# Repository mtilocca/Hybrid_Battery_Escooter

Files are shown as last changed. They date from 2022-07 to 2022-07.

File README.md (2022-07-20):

# Hybrid_Battery_Escooter
In this repository it is presented the work related to the B.sc. thesis, where an High Performance Hybrid Battery circuit was developed for an E-scooter.

In this project is presented a strategy aimed at the development of a DC-DC converter best suited to operate in an HESS configuration using HP and HE battery types in a Dual- cell architecture for E-scooter application.
The core feature of the active parallel HESS configuration proposed was represented by the development and testing of a bidirectional DC-DC converter. Which needs to operate either as a boost and either as a buck converter. Through that a 3- phase BLDC was supplied with the energy stored in the UC bank during accelerations of the ES, while it recharged the UC bank during regenerative braking.
It was first simulated the acceleration behavior of an ES. The parameters obtained from that were used for designing the DC- DC converter. According to its requirements a control algorithm was developed in Arduino. Consequently empirical tests were performed to validate the converter and the developed control algorithm.

## System Architecture 
HESS

HESSs

## PCB Schematics 
SCHEM

pcb

## Experimental Results 


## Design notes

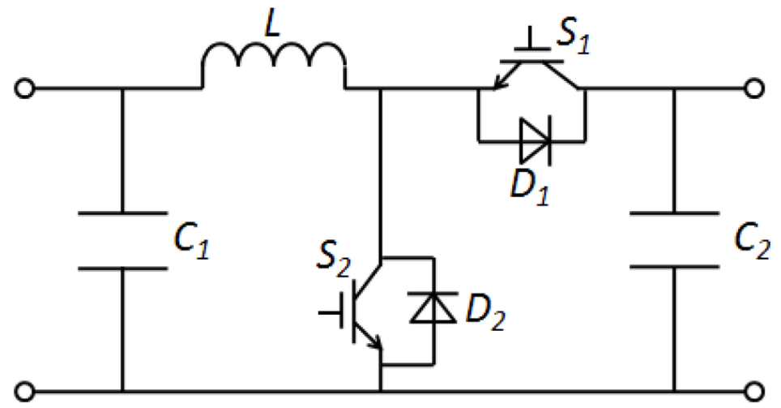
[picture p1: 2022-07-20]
Modeling/Buck Boost.PNG

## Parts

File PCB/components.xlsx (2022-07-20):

Type | PCB name | Value | Farnell code | quantity
connector |  |  | 3704683 (https://uk.farnell.com/phoenix-contact/1714955/terminal-block-wire-to-brd-2pos/dp/3704683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) | 6
connector |  |  | 3041165 (https://uk.farnell.com/phoenix-contact/1711725/terminal-block-wire-to-brd-2pos/dp/3041165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) | 9
capacitor | C4&C5&C6 | 2200u | ECA1JHG222 | 12
Mosfet |  |  | FQP85N06 (https://uk.farnell.com/infineon/irf640npbf/mosfet-n-200v-18a-to-220/dp/8648379?st=irf640) | 10
Mosfet driver | IR2110PBF |  | IR2110PBF (https://uk.farnell.com/intersil/el7104csz/driver-mosfet-single-high-speed/dp/1561928?st=el7104) | 8
connector |  |  | 31072102 | 6
capacitor | C1 & C2 | 470u | MCKSK100M471J32S (https://uk.farnell.com/united-chemi-con/ekyb800ell271mj30s/cap-270-f-80v-20/dp/2842025) | 10
Heatsink |  |  | 504222B00000G | 1
IC socket |  |  | 4814-3000-CP | 3
diode |  |  | 1N485B. | 5

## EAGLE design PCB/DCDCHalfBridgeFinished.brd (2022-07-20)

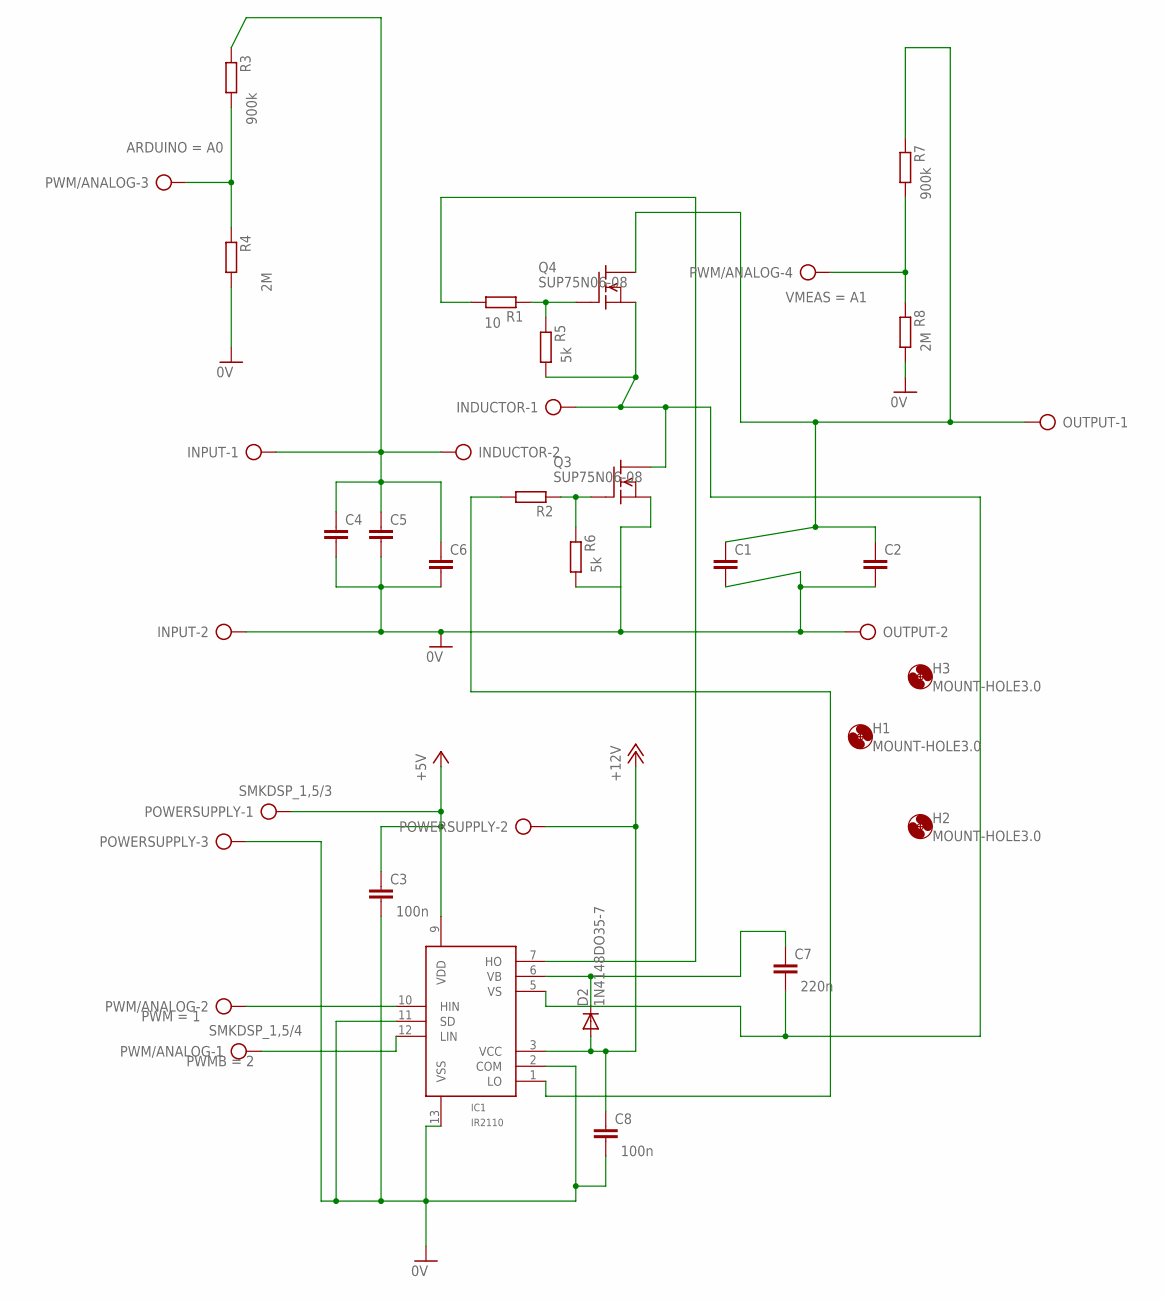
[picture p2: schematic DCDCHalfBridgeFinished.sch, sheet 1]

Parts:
C1, C2, C4, C5, C6: C-EU050-025X075; C050-025X075
C3, C7, C8: C-EU025-025X050; C025-025X050
D2: 1N4148DO35-7; DO35-7
H1, H2, H3: MOUNT-HOLE3.0; 3,0
IC1: IR2110; DIL14
INDUCTOR: AK300/2
INPUT: AK300/2
OUTPUT: AK300/2
POWERSUPPLY: SMKDSP_1,5/3
PWM/ANALOG: SMKDSP_1,5/4
Q3, Q4: SUP75N06-08; TO220
R1, R2, R3, R4, R5, R6, R7, R8: R-EU_0204/7; 0204/7

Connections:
+5V: C3.1, IC1.9 (VDD), POWERSUPPLY.1
+12V: C8.1, D2.A, IC1.3 (VCC), POWERSUPPLY.2
GND: C1.2, C2.2, C3.2, C4.2, C5.2, C6.2, C8.2, IC1.2 (COM), IC1.11 (SD), IC1.13 (VSS), INPUT.2, OUTPUT.2, POWERSUPPLY.3, Q3.3 (S), R4.2, R6.2, R8.2
unnamed: PWM/ANALOG.3, R3.2, R4.1
unnamed: IC1.12 (LIN), PWM/ANALOG.1
unnamed: IC1.10 (HIN), PWM/ANALOG.2
unnamed: C7.2, IC1.5 (VS), INDUCTOR.1, Q3.2 (D), Q4.3 (S), R5.2
unnamed: IC1.1 (LO), R2.2
unnamed: Q4.1 (G), R1.1, R5.1
unnamed: Q3.1 (G), R2.1, R6.1
unnamed: PWM/ANALOG.4, R7.2, R8.1
unnamed: C7.1, D2.C, IC1.6 (VB)
unnamed: C1.1, C2.1, OUTPUT.1, Q4.2 (D), R7.1
unnamed: IC1.7 (HO), R1.2
unnamed: C4.1, C5.1, C6.1, INDUCTOR.2, INPUT.1, R3.1

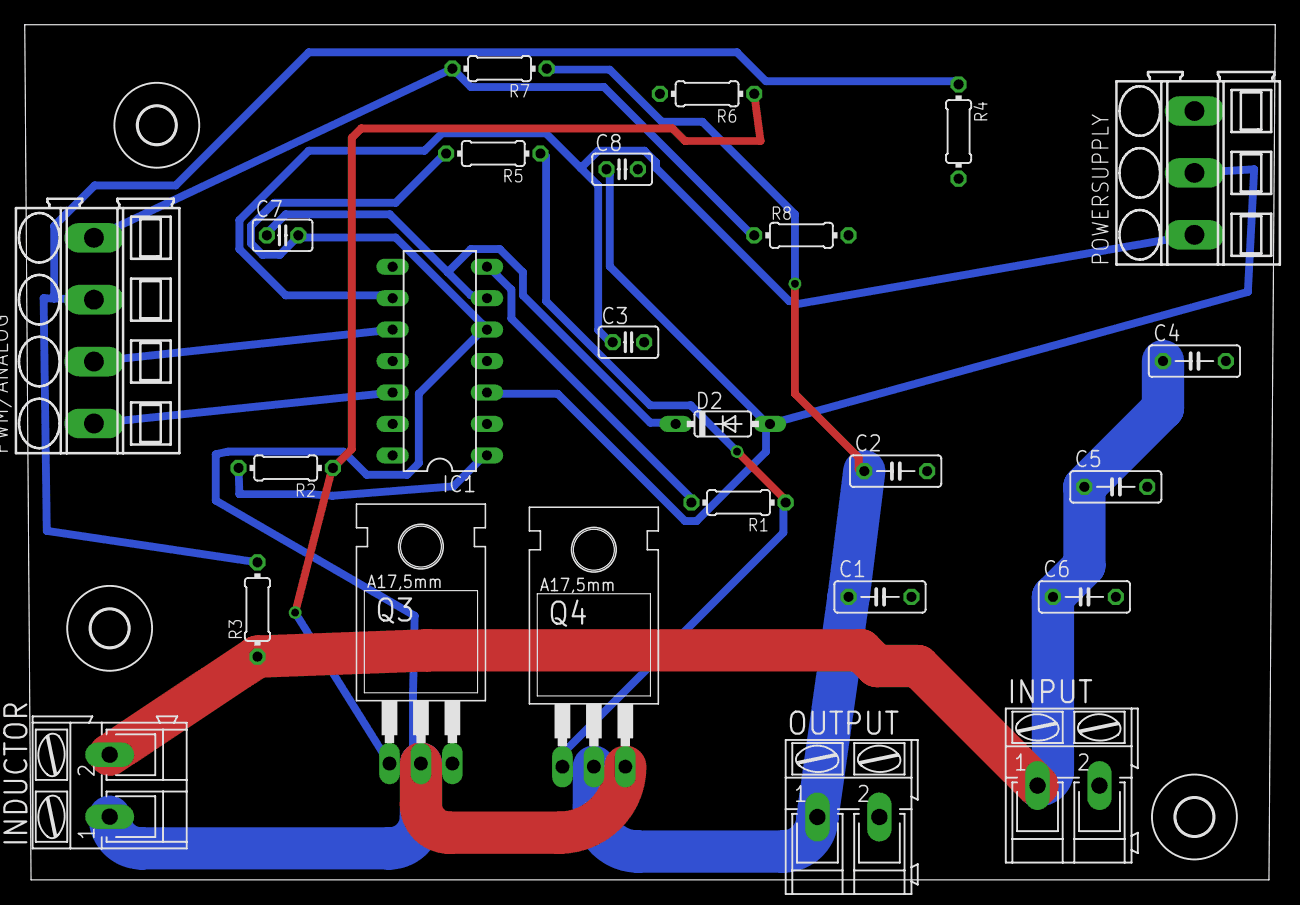
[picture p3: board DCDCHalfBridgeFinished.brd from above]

Board: 2 copper layers, 101.0 x 69.1 mm, 28 parts (0 on the bottom side), 15 nets.

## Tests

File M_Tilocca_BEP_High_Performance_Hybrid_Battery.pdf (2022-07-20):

# DC-DC converter for high performance hybrid battery applications

Mario Tilocca, Eindhoven University of Technology, Department of Electrical Engineering, ID 1034263, m.tilocca@student.tue.nl

Abstract—In this paper is presented a strategy aimed at the development of a DC-DC converter best suited to operate in an HESS configuration using HP and HE battery types in a Dual-cell architecture for E-scooter application.
The core feature of the active parallel HESS configuration proposed was represented by the development and testing of a bidirectional DC-DC converter. Which needs to operate either as a boost and either as a buck converter. Through that a 3-phase BLDC was supplied with the energy stored in the UC bank during accelerations of the ES, while it recharged the UC bank during regenerative braking.
It was first simulated the acceleration behavior of an ES. The parameters obtained from that were used for designing the DC-DC converter. According to its requirements a control algorithm was developed in Arduino. Consequently empirical tests were performed to validate the converter and the developed control algorithm.

Index Terms—E-Scooter, Hybrid Battery, HESS, Voltage Sensor, Lithium-ion Ultracapacitors, LiFePo4 battery, DC-DC converter, Half Bridge, Buck-Boost, PWM, Control Algorithm.

I. INTRODUCTION
I
N this paper is discussed about the development of a DC-DC converter which allows to integrate a dual battery architecture in E-scooters (ES) applications. The main contribution is to show an efficient energy management strategy aimed at developing and controlling a DC-DC bidirectional converter. The scope of the converter is to regulate the input and output voltage dynamically. Thus it is possible to ensure a constant output voltage, namely the nominal operating voltage of the BLDC motor used in ES, regardless of the value of the input voltage during ES accelerations. Conversely during regenerative braking the proposed control strategy enables the output voltage to vary according to the state of charge (SoC) of the high power (HP) battery topology. During this process the input voltage supplied is maintained constant throughout the duration in which the employed BLDC motor is operated as a generator. Therefore a research question arises:

What approach should be adopted when developing bidirectional DC-DC allowing to combine a dual battery architecture while ensuring to maintain high performances in ES applications ?

In the following sections of the paper it is discussed about related researches which focused on ES and battery topologies used in light electric vehicles applications. Consequently the methodologies employed and the results obtained during the development and testing of the DC-DC bidirectional converter are examined.

II. LITERATURE RESEARCH & BACKGROUND

ES are designed to be a quiet and low vibration vehicle that find their main employment in residential urban areas drastically reducing CO2 emissions and improving air quality
[1] .In recent years with the improvements in the field of a rechargeable batteries it has been possible to sensibly increase the operational range of light E-vehicles where volume constraints play a key role in the design of the E-bikes and ES particularly [2].
Therefore, one of the main challenges is developing a balanced system of different fuel-cell topologies which allows the vehicle to achieve performances and have an autonomy range comparable to scooter mounting an internal combustion engine keeping the total mass of the vehicle approximately the same.
In order to tackle this challenge a possible solution is the development of hybrid energy storage systems (HESSs) [3]. A typical HESS configuration is built using two different topologies of fuel-cells, being able to efficiently combine both High Energy (HE) and High Power (HP) characteristics [4]. In this research paper the goal is being able to develop DC-DC converter suited to operate in a Dual-Cell system which employs Lithium-Ion ultra-capacitors in particular for their HP properties together with Lithium Iron Phosphate (LiFePo4) for the HE part.
One of the main focuses is towards the charge/discharge energy efficiency which is one of the main indicators regarding the battery life cycle performance [4]. In order to achieve an higher overall efficiency of the system an important role is played by the handling of the energy during regenerative braking and standstill accelerations where the energy demand is higher compared to cruise speed.
During standstill accelerations the primary source of the energy drawn by the Brush-less DC motor of the vehicle are the lithium-ion ultracapacitors as the overall power demand in order to reach the cruise speed is high. Conversely during the part of the trip at constant speed the LiFePo4 batteries should be the main source of the energy drawn by the BLDC motor as the power demand is low but constant.
During regenerative braking the power flow is reversed, going from the BLDC motor to the fuel-cells. In this scenario the energy should be first directed to the ultracapacitors in order to recharge them [5]. Solely after the ultracapacitors are fully charged the power should be drawn by the LiFePo4 cathode battery pack as the latter has an higher internal resistance compared to the Lithium-Ion ultracapacitors. Therefore leading to higher losses which can overheat the battery damaging it. Hence in order to minimize the losses a DC-DC converter is placed between the ultracapacitors and the battery pack to allow a bidirectional power flow [6].

III. METHODS
A. Acceleration of an E-Scooter
The technology employed in the development of electric scooters have been steadily improving in recent years reaching performances analogous with the ones of internal combustion engine (ICE) scooters.
An important parameter of comparison between the ES and the ICE scooter is represented by the wide open throttle (WOT) behavior of the ES in a standstill acceleration. In order to comprehend this particular behavior a simulation of 500 data points was performed in Matlab. The constant parameters of the ES analyzed are depicted in Table I. Two separate equations were used in order to precisely simulate the behavior of the increase of velocity vn+1 of the ES according to: [2]

vn+1 = vn +δt ·(157−0.00145 · v

2
n
) | (1)

where vn is the current velocity, the aforementioned equation can be used to describe the behavior of the ES until it reaches a velocity of 10.8 m/s; afterwards Eq. 2 is used to calculate the next value of the velocity in the simulation [2].

vn+1 = vn +δt ·(7.30−0.53 · vn −0.00145 · v

2
n

) (2)

Consequently it is possible to progressively calculate the travelled distance dn+1 according to: [2]

dn+1 = dn +0.1 · vn | (3)

where, dn represents the current traveled distance. Since the ES simulation is at WOT it is assumed the acceleration a to be constant as it is depicted in the following equation:

a =

2 · dtot t
2 | (4)

where, dtot represents the total distance traveled by the scooter to reach its maximum velocity. Hence, it is possible to determine the behavior of the current drawn from the batteries by the 3-phase BLDC motor, Imotor according to Eq. 5. Thus, it is consequently possible to determine the development of traction force of the ES according to Eq. 6 [7].

Imotor =

avnm Vmotor | (5)

Ftr =

VmotorImotor

vn+1

(6)

B. Battery Topologies
In the system analyzed HP and HE battery topologies are combined together in an active parallel HESS configuration as it is shown in Fig. 1.

TABLE I
SCOOTER SIMULATION CONSTANTS
Symbol | Variable | Value | Unit
Vm | BLDC motor nominal voltage | 48 | V
m | total mass of the scooter | 180 | kg
t | total simulation time | 50 | s
δt | time sample | 0.1 | s

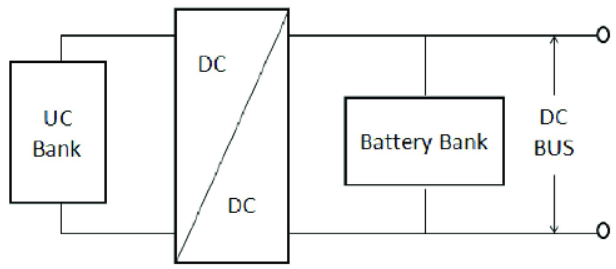
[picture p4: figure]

Fig. 1. Active parallel HESS configuration [3]

LiFePo4 cathode battery: Due to its low cost, long durability and more environmental friendly impact compared to cobalt based cathode batteries LiFePo4 have been chosen to be the HE components in the HESS configuration [8]. The specifications of a LiFePo4 fuel-cell are depicted in Table II. In order to meet the DC bus voltage requirements 16 fuel-cells are connected in series thus satisfying the nominal voltage requirement of the BLDC motor of the ES.
Thus the battery bank has a voltage ranging between 58.4 V and 40 V depending on the state of charge SoC of the battery bank.
Lithium-Ion Ultracapacitors: One of the main characteristics of the chosen ultracapacitors is their property to fully discharge in few seconds which makes them best suited to be used as source of power during accelerations of the ES [9]. Their HP characteristics are shown together with the main properties in Table III.
By contrast it is worth to note that the lithium-ion ultracapacitors have a lower energy density compared to the the LiFePo4. In the HESS configuration analyzed 10 Lithium-Ion ultracapacitors fuel-cells were connected in series, with a voltage ranging between 22 V and 38 V depending on the SoC. Which was constantly monitored via a voltage divider connected to the microcontroller.
C. DC-DC Converter
1) Converter Topologies: The main challenge in the development of an HESS configuration is the realization of a bidirectional DC-DC convert. Which allows the power to flow

TABLE II
LIFEPO4 CHARACTERISTICS [8]
Name | Value | Unit
Nominal cell voltage | 3.2 | V
Max charge voltage | 3.65 | V
Min discharge voltage | 2.5 | V
Specific Energy | 90110 | Wh/kg
Energy density | 220 | Wh/L
Specific Power | 200 | W/kg
Internal resistance | 0.1 | Ω

TABLE III
LITHIUM-ION ULTRACAPACITOR SPECIFICATIONS [9]
Name | Value | Unit
Nominal cell voltage | 2.2 -3.8 | V
Specific Energy | 11 | Wh/kg
Energy density | 19-25 | Wh/L
Specific Power | 9300 | W/kg
Internal resistance | 0.13 | Ω

TABLE IV
DC-DC CONVERTER CONSTANTS
Symbol | Variable | Value | Unit
VDC | DC bus nominal voltage | 48 | V
Vc | Ultracapacitors voltage range | 22-38 | V
fs | Switching frequency | 32000 | Hz
IDC | DC bus max current | 22.64 | A

either from the UC and battery banks to the BLDC motor and either during regenerative braking from the motor to the fuel-cells [10]. Thus creating a power buffer extends the life cycle of either the HP and HE components whilst shrinking the thermal losses.
In this particular case the DC-DC converter must work as a boost converter. Thus regulating the current UC bank voltage to the nominal DC bus voltage, during ES accelerations where the main energy source is provided by the UC bank. Conversely during braking the power recovered should be firstly directed to the UC bank until it is fully charged. Hence during this phase the DC-DC converter has to operate as a buck converter as the DC bus nominal voltage is higher than the maximum UC bank voltage, as it is shown in Table IV. For the aforementioned reasons the most suitable DC-DC converter for this application is a bidirectional buck-boost half bridge, as shown in Fig. 2.

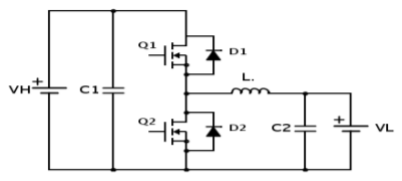
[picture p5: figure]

Fig. 2. Bidirectional Buck-Boost Half Bridge [10]

Boost Mode: When working as a boost converter, the power Mosfet Q1 shown in Fig. 2 is switched off for the whole duration of the process, while the power Mosfet Q2 is regulated according to the duty cycle Dboostobtained with the following equation:

Dboost = 1−

Vc

VDC

(7)

where Vc represents the input voltage, represented by the UC bank voltage and VDC the output voltage represented by the DC bus nominal voltage as it is shown together with the other converter constants in Table IV.

By knowing the duty cycle it is possible to design to determine the required inductance L1 using the following equation:

L1 =

VcDboost
fs∆IL

(8)

where fs represents the switching frequency and ∆IL the ripple current which can be obtained according to Eq. 9:

∆IL =

0.35 ·VDC ·IDC
Vc

(9)

where it is assumed that the ripple current is equal to 35% of the maximum output current IDC drawn by the BLDC motor. Moreover it is possible to calculate the required output capacitance C1 as shown in Eq. 10 where ∆Vrip represents the voltage ripple which is assumed to be maximum 1% of the total output voltage and it is calculated according to Eq. 11.

C1 =

IDCDboost

fs∆VripB

(10)

∆VripB = 0.01 ·VDC | (11)

Buck Mode: During regenerative braking it is assumed that the UC bank is empty as the energy in it should have been used previously during the acceleration phase.
Therefore the DC-DC converter works in buck mode in order to recharge the UC bank. Assuming a 100% efficiency it can be assumed that the power in input Pin is equal to the power in output Pout as shown in the following equations:
Pin = VDCIDC | (12)
Pin = Pout | (13)

by knowing the power in output it is possible to calculate the current which is drawn by the UC bank Ic during regenerative braking as shown in the following equation:

Ic =

Pout
Vc

(14)

During this phase the power Mosfet Q2 is switched off, while by knowing the duty cycle Dbuck as it is shown in Eq.15 of the power Mosfet Q1 showed in Fig. 2, it is possible to calculate the required inductance L2 through Eq. 16.

Dbuck =

Vc

VDC

(15)

L2 =

Vc ·(1−Dbuck)
2 · fsIc

(16)

Moreover the required output capacitance C2 can be calculated according to the following equation:

C2 =

DbuckIc

fs∆Vripb

(17)

where ∆Vripb
represents the voltage ripple which is estimated to account for 1% of the UC bank voltage as shown in the equation below.
∆Vripb = 0.01 ·Vc | (18)

D. Microcontroller Implementation & PWM Algorithm
In order to monitor the SoC of the UC bank and the voltage being supplied to or drawn by the DC bus two voltage sensors were be used. Hence two voltage dividers were directly implemented on the PCB which was connected with the employed Arduino Mega 2560. The chosen microcontroller can sense a maximum voltage of 5 V, any value above might cause irreparable damage. Therefore the resistors employed had a value of 1 kΩ and 12 kΩ respectively. Thus the microcontroller could safely sense voltages up to 65 V while maintaining an optimal current of 3.8 mA. By constantly being updated regarding the voltage of the UC bank and DC bus it was possible to estimate the SoC. Based on current SoC of the UC and DC bus the duty cycle Dboost of the power Mosfet Q2 was constantly adapted by sending a new pulse width modulation (PWM). As more power during accelerations is being drawn by the BLDC motor the voltage Vc of the UC bank is reduced and therefore the duty cycle Dboost increased.
Conversely during regenerative braking the duty cyle Dbuck was updated according to voltage of the UC bank Vc representing its SoC. Which gradually increased as the supercapacitors were being recharged.

IV. RESULTS & DISCUSSION

A. Acceleration of an E-scooter
By applying Eq.1 and Eq.2 into the Matlab tool the behavior of the velocity of the ES at WOT can be obtained as it is shown in Fig.3. In this figure it is shown how the maximum velocity obtained is around 48 km/h, which accurately represents the empirical behavior of scooters. Consequently, by applying Eq.3 and Eq.4 it was found that the acceleration a of the ES at WOT is equal to 0.483 m/s

2
. In Fig.4 it is shown the

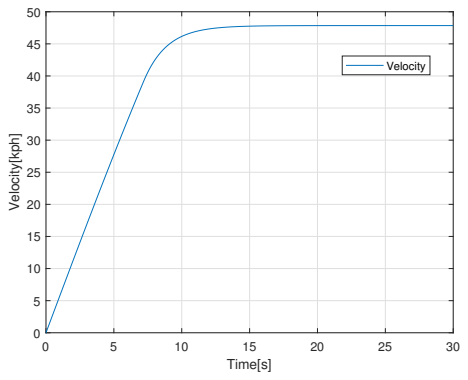
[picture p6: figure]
Time[s]; Velocity[kph]; Velocity

Fig. 3. Full power acceleration of ES

behavior of the current drawn by the BLDC motor of the ES which was obtained by applying Eq.5. It is worth mentioning that the behavior of velocity, shown in Fig.3, and the behavior of the motor current, shown in Fig. 4, are similar as they are both influenced by the acceleration a.
By comparing the velocity of the scooter and the current

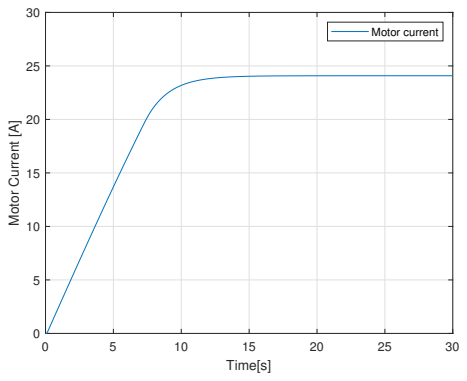
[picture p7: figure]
Time[s]; Motor Current [A]; Motor current

Fig. 4. Current drawn by the scooter motor during acceleration time

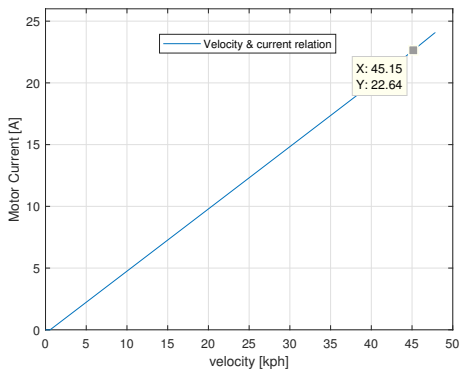
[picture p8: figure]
velocity [kph]; Motor Current [A]; Velocity & current relation

Fig. 5. Current drawn by the scooter motor with respect to velocity

drawn by its motor as it is shown in Fig.5 it is worth noting that they have a linear relation; furthermore from the aforementioned graph it was possible to determine the current drawn by the motor at 45 km/h which is the speed limit at which the scooters are allowed to drive in most EU countries. The value obtained from this graph was used as maximum motor current IDC in the DC-DC converter parameters calculations. Moreover by applying Eq.6 it was possible to simulate the

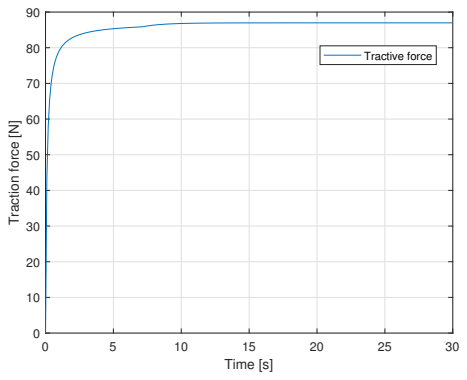
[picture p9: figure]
Time [s]; Traction force [N]; Tractive force

Fig. 6. Traction force behavior of ES at full power acceleration

TABLE V
DC-DC CONVERTER PARAMETERS
Symbol | Variable | Value | Unit
C1 | Boost output capacitance | 798 | µF
C2 | Buck output capacitance | 5600 | µF
L1 | Inductance boost | 21.5400 | µH
L2 | Inductance buck | 1.4498 | µH

behavior of the traction force Ftr of the ES as shown in Fig.6, it is worth noting that the force reaches in 10 seconds its peak value which is 87 N and it behaves steadily afterwards. The rapid growth above 80 N in less than 2 seconds has to be addressed to the constant acceleration at which the scooter is traveling. Consequently as the velocity of the scooter is higher than 10.8 m/s it slows its growth until it steadily increase to reach 87 N. Furthermore it is important to mention that the values of the traction force obtained in the simulation are similar with discrepancy of 0.34% to the gathered empirical data of a similar ES which reaches a speed of 35 km/h with a traction force of 86.7 N [7].

B. DC-DC Converter
In order to realize the DC-DC converter PCB using the software Eagle it was first needed to calculate the boost capacitance C1 and the buck capacitance C2 following Eq.10 and Eq.17 respectively as it is shown in TableV. Furthermore the respective inductors L1 for the boost mode and L2 for the buck mode were calculated according to Eq.8 and Eq.16. However since it is possible to mount only one inductor in the chosen design it was decided to build the inductor designed for the boost mode as it is larger than the minimal one needed for the buck mode as it is shown in Table V. In Fig.7 it is shown the circuitry schematics developed through the software Eagle, it was decided to use to satisfy the buck capacitance C2, 3 parallel connected ECA1JHG222 electrolytic capacitors with 2200 µF capacitance each. Whilst 2 parallel connected MCKSK100M471J32S electrolytic capacitors with 270 µF capacitance each for the boost capacitance C1.
The power Mosfet employed was the FQP85N06due to its high switching properties and its reliability at high voltages and currents. Moreover the FQP85N06 power Mosfets will receive the boosted PWM signal from the IR2110 gate driver which was connected directly to the Arduino Mega 2560. The final layout of the 2 layer PCB board designed is presented in Fig.8. The board high power traces were designed to be 0.018 mm thick and 7.62 mm wide in order to resist to a current up to 18 A. Whilst the traces concerning the gate driver and voltage dividers were designed to be 0.635 mm wide being resistant to a current up to 2.7 A. Furthermore two ground planes were designed having an minimal isolation of 1.27 mm from each trace.
V. TESTING
The proposed DC-DC converter design and control algorithm were empirically tested. In the experimental setup in addition to the Arduino Mega 2560 and the assembled PCB a 94 Ω resistor was employed as load to dissipate the

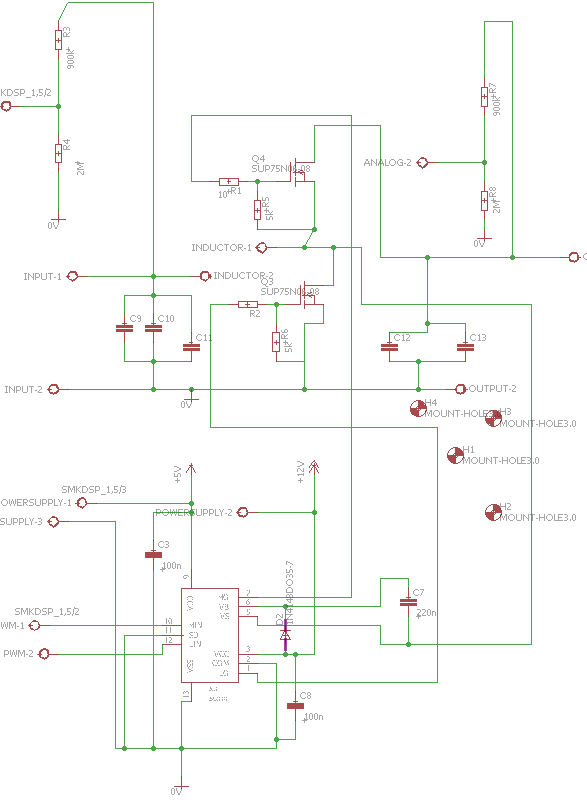
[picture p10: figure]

Fig. 7. Bidirectional buck-boost half bridge Eagle schematic

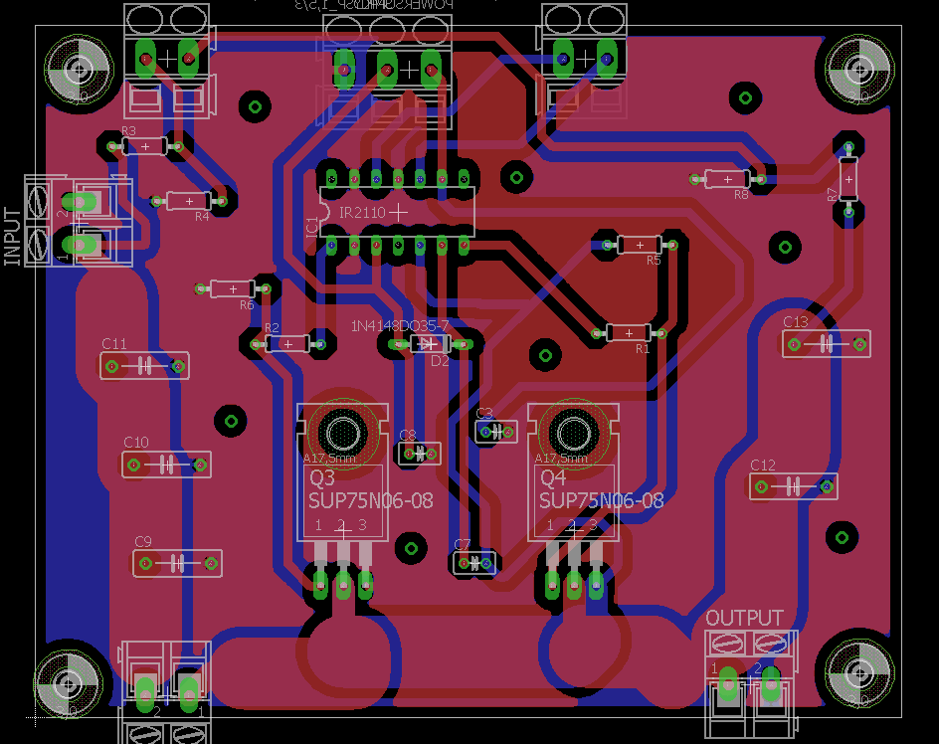
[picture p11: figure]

Fig. 8. Bidirectional buck-boost half bridge Eagle designed PCB

power while a DC voltage source was used to supply power to the circuit. Two external auxiliary DC voltage sources were employed in order to power the IR2110 gate driver. Furthermore the switching frequency was increased from 32 kHz to 62.5 kHz in order to enable higher reliability and lower losses.
Before tests involving the lithium-ion ultracapacitors could be conducted it was first tested that the converter worked in boost and buck mode with fixed duty cycles Dboost and Dbuck. In order to achieve the correct values the function which calculated the duty cycle in Arduino had to be adjusted and tuned. As these experiments were successful the control algorithm aimed at dynamically update the duty cycle could be tested. During Boost operation the DC-DC converter input voltage was gradually manually decreased ranging from 38 V to 22 V as it is shown in Fig.9.

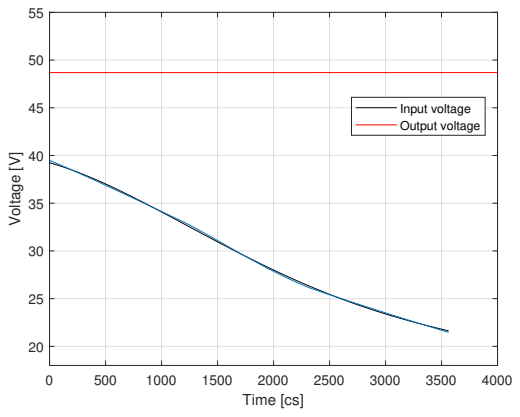
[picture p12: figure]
Time [cs]; Voltage [V]; Input voltage; Output voltage

Fig. 9. DC-DC converter input and output voltage fitted curves behavior during Boost operation

This was aimed at simulate the behavior of the ultracapacitors bank whose voltage is dropped as its SoC shrinks.
The output voltage behavior remained steady throughout the entire experiment as it is shown in Fig.9.
In this figure the behavior of the data recorded through the microcontroller has been processed in Matlab to obtain the fitted curves of the behavior of the input and output voltage. Conversely during buck operation as the power flow is reversed the input voltage is maintained steady at 48 V while the supercapacitors were being recharged. An offset 12.727% higher with respect to the initial voltage during buck operation (22 V) in the Arduino resolution was recorded as it is presented in Fig.10.
Thus during buck operation the UC bank was overcharged despite an input current of 0.82 A. Consequently this led to damaging the UC bank. However the behavior of the output voltage during buck operation shown in Fig. 10 followed the theoretical expectations as it gradually increased as the SoC of the UC bank incremented.
Hence, despite the boost operation of the converter could not be tested with the UC bank its control strategy has been successful as the behavior of the input voltage is shown in Fig.9.
As in order to obtain a steady output voltage behavior the duty cycle Dboost was successfully dynamically adjusted.

VI. CONCLUSION & REFLECTION
In this paper the behavior of an ES during full power acceleration, an HESS configuration employing a Dual-Cell fuel battery type together with a bidirectional DC-DC converter and its control and modulation strategy were presented. It has been shown that a correct implementation of the ES model has a crucial impact when determining the core parameters of the DC-DC converter. Furthermore it has been demonstrated that the proposed converter circuitry satisfied the theoretical assumptions when empirically tested. Moreover, despite the PWM control algorithm had to be adjusted and adequately tuned during the execution of the testing phase it can be said to be effective. Although the recorded data presented

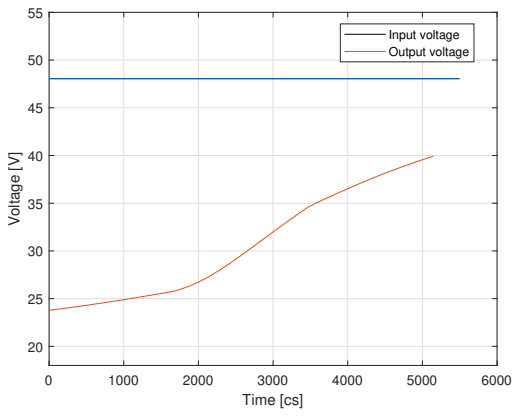
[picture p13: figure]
Time [cs]; Voltage [V]; Input voltage; Output voltage

Fig. 10. DC-DC converter input and output voltage fitted curves behavior during Buck operation

discrepancies with the expected values the executed tests were successful. Thus, it can be said that the initial research question is answered. However several improvements could be still achieved. Namely due to the inaccuracies regarding the SoC of the UC bank an improved control strategy could be formulated. The main focus should be on developing and successfully implementing an algorithm where the SoC of the UC bank is accurately monitored. Furthermore it should be able to safely interrupt the power flow towards the UC bank in buck operation in case it is satisfactorily recharged.

REFERENCES
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

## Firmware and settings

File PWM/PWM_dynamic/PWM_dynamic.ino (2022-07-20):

int Boost =4 ;
int Buck = 13;
float VoltageC = A0;
float VoltageB = A1;
float Vbat = 0;
float Vcap = 0;
int DBnorm =0;
int Dbnorm;
float Dbo ;
float Dbu ;
float k;
float j;


void setup() {
Serial.begin (9600);
int myEraser = 7;             
TCCR0B &= ~myEraser;
int myPrescaler = 1;          
TCCR0B |= myPrescaler;
}

void loop() {
Vbat = analogRead(VoltageB)*(5.0/1024.0)*13.0;
Vcap = analogRead(VoltageC)*(5.0/1024.0)*13.0;
delay(100);
Dbo = (48.0-Vcap)/48.0; 
Dbu = Vcap/48.0; 
DBnorm = ((127.0*Dbo)/0.5);
Dbnorm = ((127.0*Dbu)/0.5);

if (Dbo >= 0.21 && Dbo <= 0.54){
analogWrite(Boost, DBnorm);}
else {
analogWrite(Boost, 127); }
 //analogWrite(Buck, 0); 
Serial.println(Vcap);

//Serial.println(Vbat); 

if (Dbu >= 0.41 && Dbu <= 0.71){ 
 analogWrite(Buck, Dbnorm);}
else{
 analogWrite(Buck, Dbnorm);}

}

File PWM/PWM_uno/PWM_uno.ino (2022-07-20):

int Boost =4 ;
int Buck = 13;
float VoltageC = A0;
float VoltageB = A1;
float Vbat = 0;
float Vcap = 0;
int DBnorm =0;
int Dbnorm;
float Dbo ;
float Dbu ;
float k;
float j;



    void setup() {
//pinMode(Boost, OUTPUT);
//pinMode(Buck, OUTPUT);
Serial.begin (9600);
int myEraser = 7;             
TCCR0B &= ~myEraser;
int myPrescaler = 1;          
TCCR0B |= myPrescaler;}

    void loop() {
  
Vbat = analogRead(VoltageB)*(5.0/1024.0)*13.0;
Vcap = analogRead(VoltageC)*(5.0/1024.0)*13.0;
delay(10000);
 // if ( Vbat > 0.0 ){
  //Serial.println(Vbat); 
  //delay(15000);}
 // }
//Serial.println(Vbat);
  // delay(15000);
  //k = Vcap/48.0;
Dbo = (48.0-38.0)/48.0; 
Dbu = 38.0/48.0; 
  //Serial.println(Dbo);
  //Serial.println(k);
j = 127.0 * Dbo;
//Serial.println(j);
DBnorm = ((126.0*Dbo)/0.5)-13.5;
Dbnorm = ((127.0*Dbu)/0.5)-13.5;

//Serial.println(Dbo);
//Serial.println(DBnorm);
// Boost 
//if (Vcap >= 22.0){
//Serial.println(DBnorm);
//analogWrite(Boost, DBnorm);
 
//Serial.println(DBnorm);
//analogWrite(Buck, 0);//}
//else{
//analogWrite(Boost, 0);
//analogWrite(Buck, 0);}
//Serial.println(Dbnorm);
 //Buck 
 
//if (Vcap <= 38.0){
analogWrite(Buck, Dbnorm);
//Serial.println(Dbnorm);
Serial.println(Vbat);
delay(100);
//analogWrite(Boost, 0);}
//else{
//analogWrite(Buck, 0);
//analogWrite(Boost, 0);}} 
}
